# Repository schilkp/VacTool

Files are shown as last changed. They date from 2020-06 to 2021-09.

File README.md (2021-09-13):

# VacTool
### Philipp Schilk

A very simple PIC12F1572-based controller for a manual vacuum SMD component pick-and-place pen. 

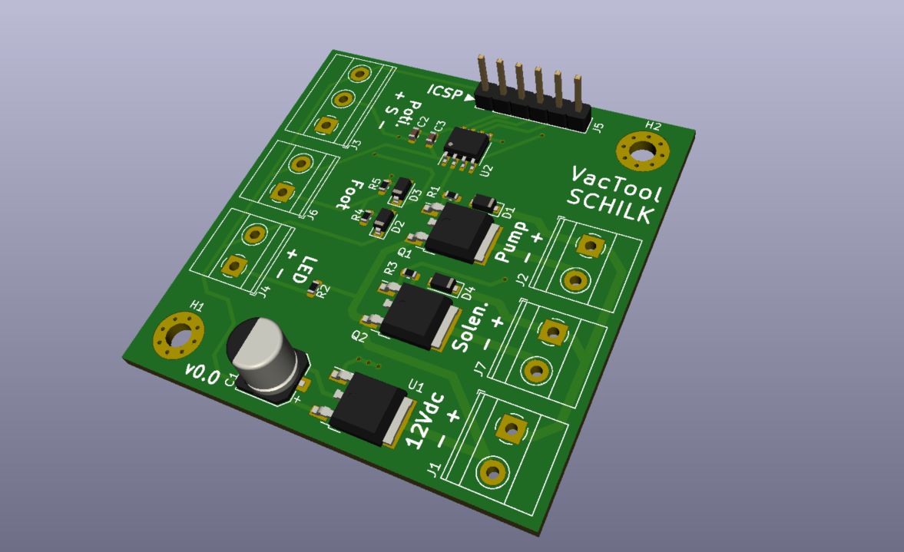
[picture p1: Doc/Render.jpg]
PCB Render


# Description
Allows control of a 12Vdc solenoid valve and air pump using a 1/4" jack foot pedal.  
The solenoid is activated when the pedal is pressed. The operation of the pump is 
controlled by the position of the potentiometer:  

When the potentiometer is fully left, the pump follows the solenoid/foot pedal exactly.  

When the potentiometer is fully right, the pump runs continously.

In between, the pump will run when the solenoid is active, and will keep running for a while 
after the solenoid closes again determined by the potentiometer position. When continously
placing parts this should allow for a smoother workflow.

# Inspiration
Steve Gardner's (aka SDG Electronics) Vaccum Pick and Place Tool:  

[Youtube Video](https://www.youtube.com/watch?v=1FnGqH_WkL4)  

[Website](https://sdgelectronics.co.uk/youtube-videos/a-diy-smd-pick-and-place-tool-for-electronics-assembly/)

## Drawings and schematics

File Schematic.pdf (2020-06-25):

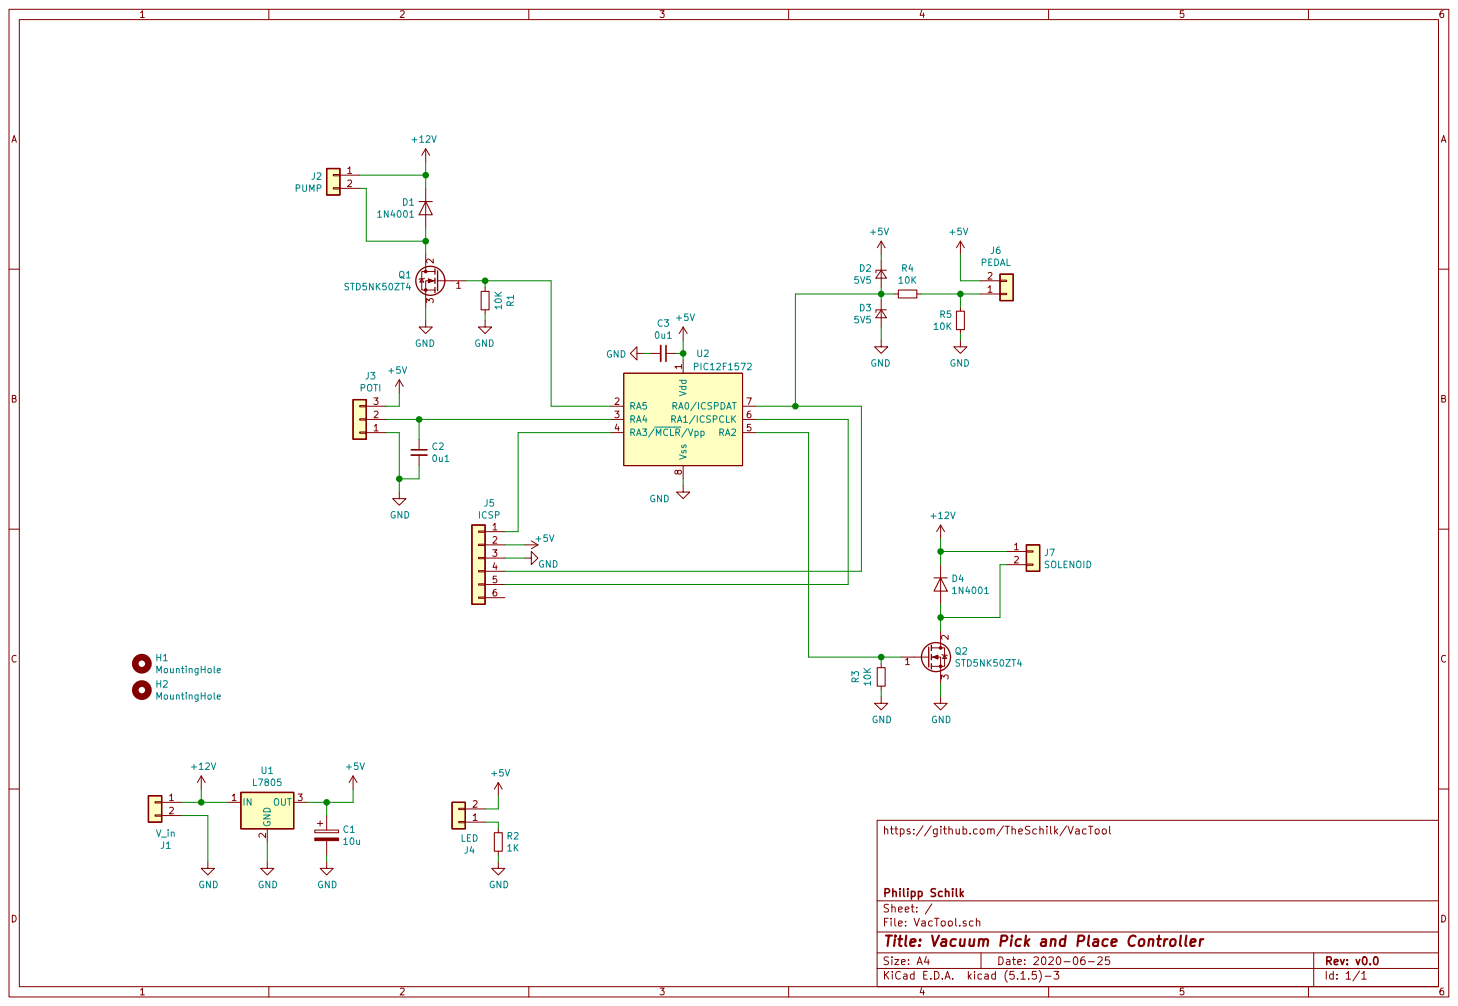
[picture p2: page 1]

1 RA5 2 RA4 3 RA3/MCLR/Vpp 4 RA2 5 RA1/ICSPCLK 6 RA0/ICSPDAT 7 Vss 8 U2 PIC12F1572 GND

https://github.com/TheSchilk/VacTool

Id: 1/1 Title: Vacuum Pick and Place Controller File: VacTool.sch Sheet: / Philipp Schilk

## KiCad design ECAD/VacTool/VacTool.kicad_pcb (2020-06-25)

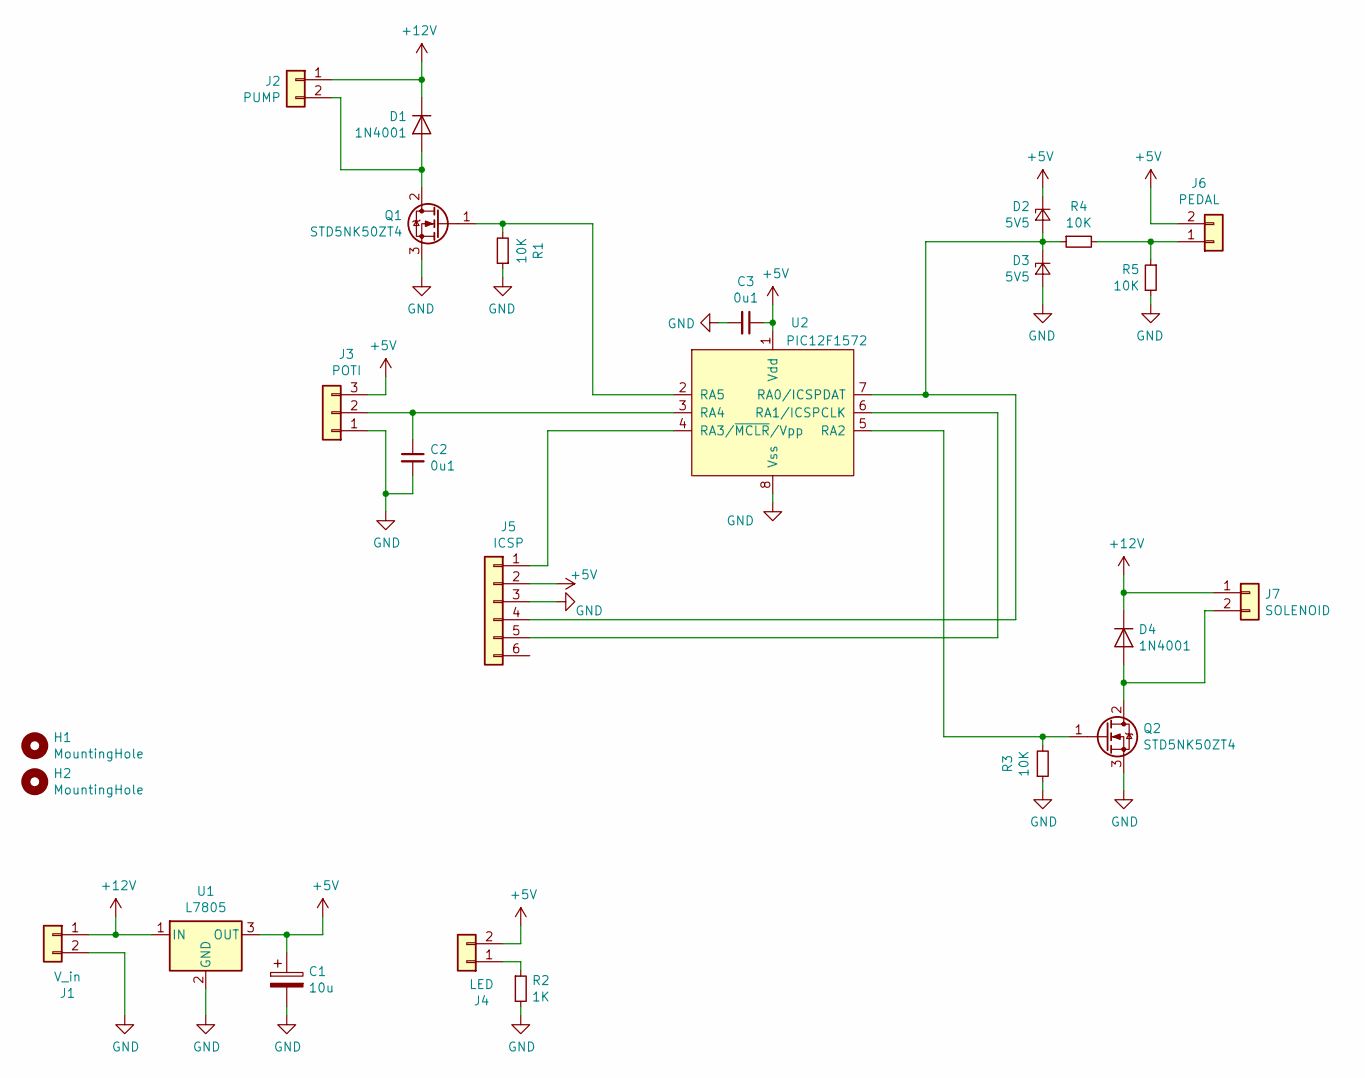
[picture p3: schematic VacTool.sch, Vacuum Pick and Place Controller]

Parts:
C1: 10u; CP_Elec_6.3x7.7
C2, C3: 0u1; C_0603_1608Metric
D1, D4: 1N4001; D_SOD-123F
D2, D3: 5V5; D_SOD-123
H1, H2: MountingHole; MountingHole_3.2mm_M3_Pad_Via
J1: V_in; TerminalBlock_Phoenix_MKDS-1,5-2_1x02_P5.00mm_Horizontal
J2: PUMP; TerminalBlock_Phoenix_MKDS-1,5-2_1x02_P5.00mm_Horizontal
J3: POTI; TerminalBlock_Phoenix_MKDS-1,5-3_1x03_P5.00mm_Horizontal
J4: LED; TerminalBlock_Phoenix_MKDS-1,5-2_1x02_P5.00mm_Horizontal
J5: ICSP; PinHeader_1x06_P2.54mm_Vertical
J6: PEDAL; TerminalBlock_Phoenix_MKDS-1,5-2_1x02_P5.00mm_Horizontal
J7: SOLENOID; TerminalBlock_Phoenix_MKDS-1,5-2_1x02_P5.00mm_Horizontal
Q1, Q2: STD5NK50ZT4; TO-252-2
R1, R3, R4, R5: 10K; R_0603_1608Metric
R2: 1K; R_0603_1608Metric
U1: L7805; TO-252-2
U2: PIC12F1572; SOIC-8_3.9x4.9mm_P1.27mm

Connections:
+5V: C1.1, C3.1, D2.1 (K), J3.3, J4.2, J5.2, J6.2, U1.3 (OUT), U2.1 (Vdd)
+12V: D1.1 (K), D4.1 (K), J1.1, J2.1, J7.1, U1.1 (IN)
GND: C1.2, C2.2, C3.2, D3.2 (A), J1.2, J3.1, J5.3, Q1.3 (S), Q2.3 (S), R1.1, R2.2, R3.1, R5.2, U1.2 (GND), U2.8 (Vss)
unnamed: C2.1, J3.2, U2.3 (RA4)
unnamed: D1.2 (A), J2.2, Q1.2 (D)
unnamed: D2.2 (A), D3.1 (K), J5.4, R4.1, U2.7 (RA0/ICSPDAT)
unnamed: D4.2 (A), J7.2, Q2.2 (D)
unnamed: J4.1, R2.1
unnamed: J5.1, U2.4 (RA3/~MCLR~/Vpp)
unnamed: J5.5, U2.6 (RA1/ICSPCLK)
unnamed: J6.1, R4.2, R5.1
unnamed: Q1.1 (G), R1.2, U2.2 (RA5)
unnamed: Q2.1 (G), R3.2, U2.5 (RA2)

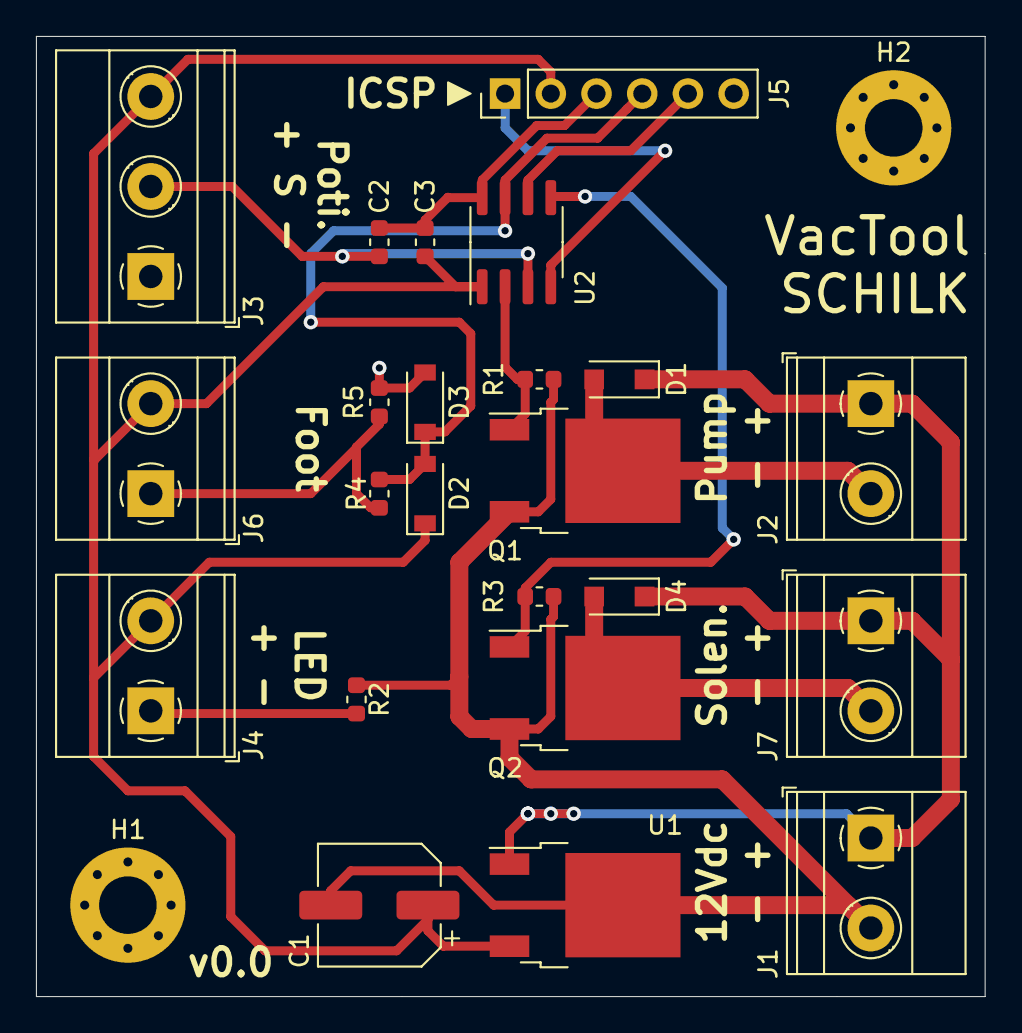
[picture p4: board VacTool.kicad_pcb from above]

Board: 2 copper layers, 52.7 x 53.3 mm, 25 parts (0 on the bottom side), 13 nets.

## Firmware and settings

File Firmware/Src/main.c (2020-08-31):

/* 
 * File:   main.c
 * Author: pschilk
 *
 * Created on June 24, 2020, 8:34 AM
 */

// CONFIG1
#pragma config FOSC = INTOSC    // (INTOSC oscillator; I/O function on CLKIN pin)
#pragma config WDTE = ON        // Watchdog Timer Enable (WDT enabled)
#pragma config PWRTE = OFF      // Power-up Timer Enable (PWRT disabled)
#pragma config MCLRE = ON       // MCLR Pin Function Select (MCLR/VPP pin function is MCLR)
#pragma config CP = OFF         // Flash Program Memory Code Protection (Program memory code protection is disabled)
#pragma config BOREN = ON       // Brown-out Reset Enable (Brown-out Reset enabled)
#pragma config CLKOUTEN = OFF   // Clock Out Enable (CLKOUT function is disabled. I/O or oscillator function on the CLKOUT pin)

// CONFIG2
#pragma config WRT = OFF        // Flash Memory Self-Write Protection (Write protection off)
#pragma config PLLEN = OFF      // PLL Enable (4x PLL disabled)
#pragma config STVREN = ON      // Stack Overflow/Underflow Reset Enable (Stack Overflow or Underflow will cause a Reset)
#pragma config BORV = LO        // Brown-out Reset Voltage Selection (Brown-out Reset Voltage (Vbor), low trip point selected.)
#pragma config LPBOREN = OFF    // Low Power Brown-out Reset enable bit (LPBOR is disabled)
#pragma config LVP = ON         // Low-Voltage Programming Enable (Low-voltage programming enabled)

#include <pic.h>
#include <stdint.h>

#define DEBOUNCE_TIME  10 // Time inputs are ignored after input in 10s of ms
#define PUMP_DIR_THR   33
#define PUMP_SCALE     6
#define PUMP_PERM_THR  0x3F0

// Pump modes
typedef enum{
    direct,   // Pump on if solenoid on
    timeout,  // Pump runs when solenoid off until timed-out
    permanent // Pump always runs
} PUMP_MODE_T;

uint32_t debounce_count;
uint8_t debounce_prevstate;
uint32_t pump_timeout_coumt; 
uint32_t pump_timeout;
PUMP_MODE_T pump_mode;
uint8_t solenoid_on;

int main(int argc, char** argv) {
    CLRWDT();
    
    // ===== WDT & CLK =====
    // Using internal MF OSC at 500khz
    OSCCONbits.SPLLEN = 0;
    OSCCONbits.IRCF = 0b0111;
    OSCCONbits.SCS = 0b10;
    
    // Have WDT reset every 512ms
    WDTCONbits.WDTPS = 0b01001;
    
    // ===== Config GPIO =====
    TRISAbits.TRISA0 = 1; // Pedal Input
    TRISAbits.TRISA2 = 0; // Valve Ouput
    TRISAbits.TRISA4 = 1; // Poti Input
    TRISAbits.TRISA5 = 0; // Motor Output
    
    // Clear all outputs
    LATA = 0x0; 
    
    // Set RA4 as only analog input
    ANSELA = 0x0;
    ANSELAbits.ANSA4 = 1;
    
    // Disable all pullups, all pins push-pull,
    // no slewrate limiting
    WPUA = 0x0;
    ODCONA = 0x0;
    SLRCONA = 0x0;
    
    // ===== Config ADC ======
    ADCON0bits.CHS = 0b00011; // Select CH3 (RA4)
    
    ADCON1bits.ADFM = 1; // Right-justified result
    ADCON1bits.ADCS = 0b000; // Conversion Clk Fosc/2
    ADCON1bits.ADPREF = 0b00; // VDD is positive voltage refernce
    
    ADCON2bits.TRIGSEL = 0; // No Automatic triggering
    
    ADCON0bits.ADON = 1; // Turn on ADC
    
    ADCON0bits.GO = 1; // Start conversion
    
    // ===== Setup Variables =====
    debounce_count = 0;
    debounce_prevstate = PORTAbits.RA0;
    pump_timeout_coumt = 0;
    solenoid_on = 0;
    
    // ===== Config Regular interrupt =====
    // Setup Timer 0 to overflow at aprox. 120Hz and trigger interrupt
    OPTION_REGbits.TMR0CS = 0; // Timer 0 clocked from Fosc/4
    OPTION_REGbits.PSA = 0;    // Timer 0 has prescalar
    OPTION_REGbits.PS = 0b01;  // Timer 0 prescalar is /4
    
    INTCONbits.GIE = 1;    // Interupts enabled.
    INTCONbits.TMR0IE = 1; // Timer 0 interrupt enabled
    
    
    while(1){
        NOP();
    }
    return (EXIT_SUCCESS);
}

void __interrupt() ISR(void){
    CLRWDT(); // pet the watchdog..
    
    // Handle ADC
    if(!ADCON0bits.GO_nDONE){
        // ADC Conversion finished
        uint16_t result = (ADRESH << 8) | ADRESL;
        
        if(result >= PUMP_PERM_THR){
            pump_mode = permanent;  
            pump_timeout = 0;
        } else if(result <= PUMP_DIR_THR){
            pump_mode = direct;
            pump_timeout = 0;
        } else {
            pump_mode = timeout;
            pump_timeout = result * PUMP_SCALE;
        }
        
        // Start next conversion
        ADCON0bits.GO_nDONE = 1;
    }
    
	// Handle De-bounce/Solenoid
	if(debounce_count == 0){ // Ready for next event
        // Determine if input changed and we should time out again
        if(debounce_prevstate != PORTAbits.RA0){
            debounce_count = DEBOUNCE_TIME;
        }
        debounce_prevstate = PORTAbits.RA0;
        
        // If the pedal is pressed, open the solenoid 
        // and keep reseting the pump timeout
        if(PORTAbits.RA0){
            LATAbits.LATA2 = 1; // Open solenoid
            pump_timeout_coumt = pump_timeout;
            solenoid_on = 1;
        } else {
            LATAbits.LATA2 = 0; // Close solenoid
            solenoid_on = 0;
        }
        
    } else { // Still timed out
        debounce_count--;
    }
        
    // Turn on/off pump
    if(solenoid_on){
        LATAbits.LATA5 = 1; // start pump
    } else if(pump_mode == permanent){
        LATAbits.LATA5 = 1; // start pump
    } else if (pump_mode == timeout && pump_timeout_coumt != 0){
        LATAbits.LATA5 = 1; // start pump
    } else {
        LATAbits.LATA5 = 0; // stop pump
    }
    
    // Handle pump timeout
    // If potentiometer was decreased during timeout, shorten. 
    if(pump_timeout_coumt > pump_timeout){
        pump_timeout_coumt = pump_timeout;
    }
    if(pump_timeout_coumt != 0){
        pump_timeout_coumt--;
    }
    
    
    // Clear flags and reset GIE
    INTCONbits.TMR0IF = 0;
    INTCONbits.GIE = 1;
}

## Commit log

2020-06-25 Initial v0.0 commit
    [VacTool-B_Cu.gbr, VacTool-B_Mask.gbr, VacTool-B_Paste.gbr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]
2020-06-25 Added PCB render
2020-08-31 Reorganised, added interactive BOM.
    [VacTool-B_Cu.gbr, VacTool-B_Mask.gbr, VacTool-B_Paste.gbr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]
